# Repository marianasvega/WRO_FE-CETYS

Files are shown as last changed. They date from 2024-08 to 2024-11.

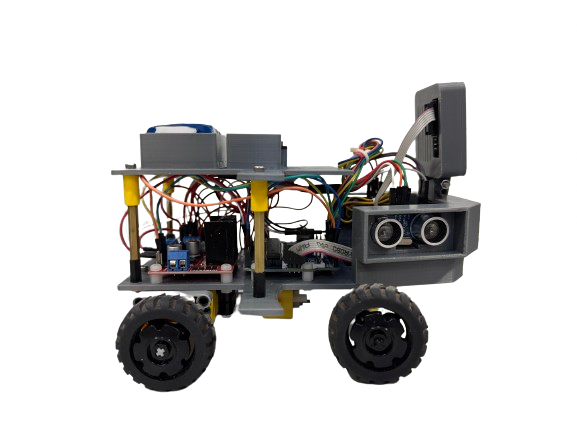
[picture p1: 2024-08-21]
Vehicle Photos/MEXICAN NATIONAL COMPETITION/Right_Side_ViewS.png

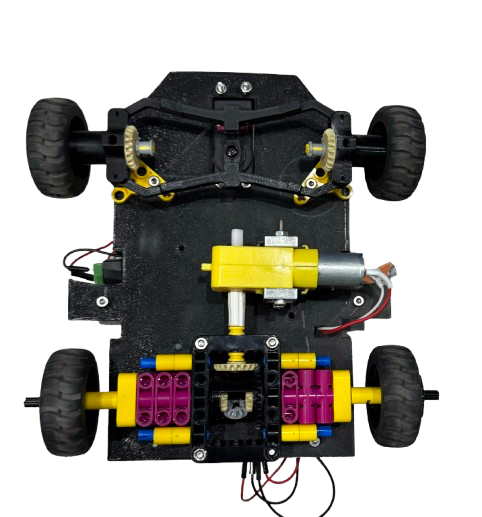
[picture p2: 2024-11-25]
Vehicle Photos/TÜRKIYE INTERNATIONAL COMPETITION/Bottom_View.png

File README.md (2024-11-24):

** **

# CETYS FUTURE ENGINEERS 2024 🤖

This is the official repository for the CETYS Team that participated in the Future Engineers category at the 2024 Mexican National and will soon compete in the International Final in Izmir, Türkiye! Here we will upload all of the processes, improvements, and results regarding our autonomous vehicle, as well as a full report on the code used and its electrical components.
  
**Team Members:** Mariana Sofia Vega Contreras, Claudio Iván López Valle & Mariana Flores Martínez.

CETYS 1 (1920 x 800 px) (1920 x 500 px)

<br>

** **

# Content
* `Models` Files for models used by 3D printers to produce the vehicle elements.
* `Others` Links of videos to understand how to prepare the vehicle for the competition. 
* `Schemes` Diagrams of the electromechanical components used in the vehicle and how they connect.
* `Src` Contains source codes for all components which were programmed to participate in the competition.
* `Team Photos` Contains 2 photos of the team.
* `Vehicle Photos` Contains 6 photos of the vehicle.
* `Video` Contains the link to a video where a driving demonstration exists.
<br>

** **

# Introduction 👷‍♀👨‍💻👩‍🔧
<br>

<div style="display: flex; align-items: flex-start;">
  ARTURO
  <p><be>This report outlines the design, development, and performance of Arturo, the autonomous vehicle developed by our team, the CETYS Future Engineers, for the 2024 World Robot Olympiad. This document will provide a comprehensive overview of our previous work in the Mexican national competition, where we successfully showcased our prototype and the iterative improvements we made in preparation for the international championship in Türkiye.
</p>
</div>
<br>
<br>

** **

# Electronic components

| Component | Quantity |
| --- | :---: |
| **ESP-WROOM-32** | 1 |
| **Bread Board Mini** | 1 |
| **Servo HS-322HD** | 1 |
| **Ultrasonic Sensor HC-SR04** | 5 | 
| **Faulhaber-type DC Motor** | 1 |
| **H-bridge Motor Driver L298N** | 1 |
| **Pushbutton** | 1 |
| **11.1V Battery 4000mAh** | 1 |
| **7.4V Battery 1000mAh** | 1 |
| **330Ω Resistor** | 1 |
| **HuskyLens Camera** | 1 |
| **Switch Button Interruptor KCD1**  | 2 |
| **Gyro + Accelerometer MPU-6050** | 1 |

<br>

** **

# Mechanism explanation

### `Robot´s Vision (HuskyLens Camera) 📷`

<div style="display: flex; align-items: flex-start;">
  HuskyLens Camera
  <p>
    For our vehicle to better detect the obstacles on the rink, we decided to upgrade from the Pixy2 Camera to the HuskyLens Camera. This decision was made after much research and due to a compatibility problem we had while trying to program the Pixy2 with the ESP32. HuskyLens is an AI-powered vision sensor designed for a wide range of applications, including robotics, DIY electronics, and IoT projects such as this. This compact camera module integrates machine learning algorithms to perform tasks like face detection, object tracking, color identification, and gesture recognition, enabling intuitive interaction and intelligent automation. For this component, we used the following code (the syntax of the commands corresponds to the HuskyLens Arduino library):
  </p>
</div>

```ruby
if (huskylens.request()) {                                        // REQUEST DETECTED OBJECTS FROM CAMERA //
    for (int i = 0; i < huskylens.countBlocks(); i++) {
      HUSKYLENSResult result = huskylens.getBlock(i);             // CHECK IF THE DETECTED COLOR IS RED OR GREEN //
      if (result.ID == 1) {                                       // GREEN COLOR (BASED ON OUR PROGRAMMING) //
        Serial.println("Detected Green Object!");
        Serial.println("X Position: " + String(result.xCenter));
      }
      else if (result.ID == 2) {                                  // RED COLOR (BASED ON OUR PROGRAMMING) //
        Serial.println("Detected Red Object!");
        Serial.println("X Position: " + String(result.xCenter));
     }
   }
 }
```

<br>
  
One of the main benefits of HuskyLens is its ability to bring sophisticated AI and machine learning capabilities to users without requiring deep technical expertise. It can also perform real-time tasks without an internet connection, leading to faster response times and reduced latency. Finally, it is compatible with various microcontrollers and development platforms, such as Arduino, ESP32, and Raspberry Pi, and supports multiple communication protocols, including UART and I2C.

<br>
<br>
  
### `Front Tire Axle (Ackerman Steering and HS-322HD Servo) 🛞`

During the Mexican National Competition, we observed that our vehicle needed a better steering system that could round corners with much more facility and precision. After much research, we learned about a mechanism named the Ackerman Steering Principle. When a vehicle turns, the inner wheel follows a tighter path than the outer wheel. To ensure smooth turning without excessive tire wear or slipping, the inner wheel needs to turn at a sharper angle than the outer wheel. This is precisely what the Ackermann geometry achieves.

<br>

<div style="display: flex; align-items: flex-start;">
  Four-Wheel Steering Design
  <p>
    <strong>Figure 1:</strong> Design and Development of Four-Wheel Steering for All Terrain Vehicle (Vishnu 2020):  
    When a driver turns the steering wheel, the motion is passed through the steering column to the steering gear. This gear changes the rotation into a pushing or pulling movement, which is sent to the tie rods. The tie rods then adjust the steering arms connected to the wheels. This setup ensures that the inside wheel turns at a sharper angle than the outside wheel, helping the vehicle turn more efficiently while reducing tire wear and slip.
  </p>
</div>

<br>

> [!NOTE]
>For the STL files to print the Ackerman system we used, visit the following link for it is NOT of our property and we give full credits to the owner: [https://github.com/KarenWon9/WRO-FI-Team-Spark](url)

<br>

<div style="display: flex; align-items: flex-start;">
  HS-322HD Servo
  <p>
    On the other hand, the HS-322HD is a popular heavy-duty servo known for its durability and performance, and without it, our vehicle would have no direction. It features Hitec's Karbonite gear train, which is significantly stronger than standard nylon gears, making it suitable for various applications. With a good balance of speed and torque, the HS-322HD is often used in RC airplanes, helicopters, and other models. To use the servo in the code, it is necessary to include the "Servo.h" library. After that, all that it takes to change the servo's angle is the following command.
  </p>
</div>

```ruby
servo.write(45);
```
<br>
<br>

### `Ultrasonic Sensors (HC-SR04) 📏`
The primary challenge in this category is navigating corners and avoiding collisions with walls. To address this, we employed the HSR04 ultrasonic sensor, which operates by emitting ultrasonic pulses and measuring the time it takes for the echoes to return after bouncing off an object. This time delay is then converted into a distance measurement, allowing the sensor to detect objects and measure distances with precision accurately. 

<br>

<div style="display: flex; align-items: flex-start;">
  Ultrasonic Sensor
  <p>
    Our autonomous vehicle uses 3 ultrasonic sensors in the front part. We have a middle sensor that is always facing forward (parallel to any wall when driving straight), the other two are positioned perpendicular to the first, one on the left side and the other to the right. These two “side” ultrasonic sensors are what help us know at any moment if we're driving too close to a wall or if a turn is near. To keep our driving as straight as possible, we added two extra ultrasonics, each one collinear to a side sensor. For a better understanding of how each sensor is positioned, please visit our <strong>Vehicle Images</strong> section.
  </p>
</div>

<br>

The HSR04 sensor typically has a range of 2 centimeters to 4 meters and is favored for its ease of integration with microcontrollers like Arduino due to its simplicity and cost-effectiveness. Its compact design and straightforward interface make it ideal for applications involving obstacle detection, proximity sensing, and distance measurement in various DIY and industrial projects. To process and interpret this signal given in centimeters, we use the following code:

<br>

```ruby
long DisCalc(int TP, int EP) {

  digitalWrite(TP, LOW);                    // CLEAR THE TRIG PIN //
  delayMicroseconds(2); 

  digitalWrite(TP, HIGH);                   // SET THE TRIG PIN HIGH FOR 10 MICROSECONDS //
  delayMicroseconds(10);
  digitalWrite(TP, LOW);

  long duration = pulseIn(EP, HIGH);        // READ THE ECHO PIN AND CALCULATE THE DIRECTION //

  long distance = duration * 0.034 / 2;     // CALCULATE THE DISTANCE IN CENTIMETERS //

  return distance;
}
```
<br>

> [!NOTE]
>The "distance" variable represents the distance from the sensor to the wall. It’s computed by multiplying the duration of the echo by the speed of sound (0.034 cm/µs) and dividing by 2 to account for the round trip of the sound wave. This distance helps in determining when to navigate around obstacles.
<br>
<br>

### `Gyro + Accelerometer (MPU-6050) 📐`
In both the open and the obstacle avoidance challenge, the vehicle must automatically stop after completing three full rounds. To accomplish this, we decided to use a combination of an accelerometer and a gyroscope. The accelerometer tracks the vehicle’s movement and angle, helping confirm its motion along the course, while the gyroscope measures precise angular changes, allowing us to identify each turn with accuracy.

<br>

<div style="display: flex; align-items: flex-start;">
  MPU-6050 Gyroscope
  <p>
    Using the gyroscope, each directional change of the vehicle is logged based on its orientation. Specifically, a 90° change corresponds to a left turn, while a -90° change corresponds to a right turn. This setup allows us to monitor every turn the vehicle makes throughout its path. By counting these 90° increments, we can accurately detect each completed round, ensuring reliable tracking over multiple rounds. Once the vehicle has completed three rounds, this data is used to signal an automatic stop.
  </p>
</div>

<br>

To achieve this, the following code uses the MPU6050.h library to read data from the MPU6050 gyroscope and accelerometer. It tracks changes in the yaw angle, incrementing by 90° with each turn. By monitoring these increments, the program counts full rotations and stops the vehicle after it reaches the target round count:

<br>

```ruby
MPU6050 mpu;                 // INITIALIZE MPU 6050 //

float ANG = 0;               // VARIABLE TO STORE YAW ANGLE //
unsigned long lastTime = 0;  // STORE THE LAST TIME TIME readYawAngle WAS CALLED //

void setup() {
  Serial.begin(115200);
  
  Wire.begin(21, 22);        // INITIALIZE I2C - SDA, SCL FOR ESP32 //

  // INITIALIZE MPU6050 ACCELEROMETER/GYRO // 
  if (!mpu.begin(MPU6050_SCALE_2000DPS, MPU6050_RANGE_2G)) {
    Serial.println("Could not find MPU6050");
    while (1);
  }
  Serial.println("MPU6050 initialized");
  
  mpu.calibrateGyro();       // SET ZERO REFERENCE FOR YAW //

  lastTime = millis();       // INITIALIZE lastTime //
}

void loop() {
  ANG = readYawAngle();      // GET THE CURRENT YAW ANGLE //
  Serial.print("Yaw Angle: ");
  Serial.println(ANG);

  // CHECK IF A 90-DEGREE TURN HAS BEEN MADE //
  if (ANG >= 90.0 || ANG <= -90.0) {
    Serial.println("90-degree turn detected!");
    ANG = 0;                 // RESET YAW ANGLE //
}
delay(10);
}

float readYawAngle() {
  Vector rawGyro = mpu.readRawGyro();
  float YR = rawGyro.ZAxis/130.0;       // CORRECT SENSITIVITY FOR 2000DPS RANGE //
  
  unsigned long currentTime = millis(); // CALCULATE TIME DIFFERENCE IN SECONDS //
  float dt = (currentTime - lastTime)/1000.0; // CONVERT TO SECONDS //
  lastTime = currentTime;                     // UPDATE lastTime FOR NEXT CALL //  
  
  float driftRate = .02 / 3.0;   // DRIFT RATE OF 1 DEGREE EVERY 3 SECONDS //
  // INTEGRATE YAW RATE OVER TIME TO GET YAW ANGLE //
  ANG += YR * dt;
  ANG -= driftRate * dt;         // Subtract the estimated drift

  return ANG;
}
```
<br>
<br>

### `Rear Tire Axle (Faulhaber MOT-165 and LEGO Differential) ⚙️`
The most crucial mechanism of any vehicle is its drive system, and we aimed to replicate this as closely as possible. After some trial and error during the building process, we decided to incorporate a LEGO differential kit to simulate real-world driving dynamics (you can find the kit [here](https://www.amazon.com/dp/B0C4LFN1HD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)). In the video provided, you can see our custom differential in action, where we designed and attached additional LEGO components. For a step-by-step guide on building your own, please refer to the "Others" folder in this repository.

<br>

<div align="center">
  <video width="340" src="https://github.com/user-attachments/assets/d7e541df-3d19-4036-9754-b866e7325a33
" controls width="600">
  </video>
</div>

<br>

> [!NOTE]
>If you want to learn how a differential works you can watch [this](https://www.youtube.com/watch?v=K4JhruinbWc) video, basically a differential gear allows wheels on the same axle to rotate at different speeds. It works by using a set of gears to distribute torque between the wheels, enabling them to turn at different rates, which is essential for smooth cornering. If 𝑇 is the total torque supplied by the engine to the differential, and it is divided between the two wheels, then the torque 𝑇<sub>1</sub> on one wheel and 𝑇<sub>2</sub> on the other wheel satisfy 𝑇 = 𝑇<sub>1</sub> + 𝑇<sub>2</sub>.

<br>

The motor used in this mechanism is a Faulhaber MOT-165. We opted for this motor because it usually operates at voltages ranging from 6V to 12V, the speed of the motor varies with voltage and load conditions, but it is designed to achieve high RPM (revolutions per minute), and it provides a modest amount of torque, suitable for small, precise applications. It is important to mention that the motor and its driver, the L298N dual H-Bridge, have their power supply, a _**Li-Po battery of 1000 mAh and 7.4V**_.
<br>

<br>

** **

## How it all comes together (explaining the code) 💻
<br>

We will now discuss how all of the previously mentioned mechanisms assemble together in our final code (Open and Obstacle Challenge). Before we start, we will show all of the functions used along the code to use as reference for when they appear next.

```ruby
int DisCalc(int TP, int EP) {                                                // ULTRASONIC BASIC CODE //

  long duration = -1;
  int reading = 120; 
  int cont = 0;

  while (cont < 5) { 
    digitalWrite(TP, LOW);
    delayMicroseconds(2);
    digitalWrite(TP, HIGH);
    delayMicroseconds(10);
    digitalWrite(TP, LOW);

    duration = pulseIn(EP, HIGH, 10000); 

    if (duration > 0) {
      reading = duration * 0.034 / 2; 
      break;  
    }

    cont++;  
  }

  return reading;

}

void printDistances(long distanceLeft, long distanceHleft, long distanceMid, long distanceHright, long distanceRight){

  Serial.print("Dis Left: ");
  Serial.print(distanceLeft);
  Serial.print(" Dis MidLeft: ");
  Serial.print(distanceHleft);
  Serial.print(" Dis Mid: ");
  Serial.print(distanceMid);
  Serial.print(" Dis MidRight: ");
  Serial.print(distanceHright);
  Serial.print(" Dis Right: ");
  Serial.println(distanceRight);

}

void printDistancesM(long distanceMid) {

  Serial.print(" Dis Mid: ");
  Serial.println(distanceMid);

}

float readYawAngle(int X) {                                                  // GYROSCOPE BASIC CODE //

  Vector rawGyro = mpu.readRawGyro();
  float YR = rawGyro.ZAxis / 131.0; 
  
  if (X == 0){
    unsigned long currentTime = millis();
    float dt = (currentTime - lastTime) / 1000.0; 
    lastTime = currentTime; 

    ANG += YR * dt;
    ANG -=   .02;  
  }

  else if (X == 1){
    unsigned long currentTime = millis();
    float dt = (currentTime - lastTime) / 1000.0; 
    lastTime = currentTime; 
  
    ANG += YR * dt;
    ANG +=   0.019;  
  }

  else if (X == 2) {
    unsigned long currentTime = millis();
    float dt = (currentTime - lastTime) / 1000.0; 
    lastTime = currentTime; 
  
    ANG += YR * dt;
    ANG -=   .075;  
  }
  
  return ANG;

}

void GreenO(int X){                                                           // OBJECT DETECTED IS GREEN //

  Serial.println("Detected Green Object!");

  if (X < 90 ){
    while(X < 90){
      SLIGHTLY_LEFT_MAX();
    } 
  }

  else if(X < 158 && X > 90){
    while(X < 158 && X > 90){
      SLIGHTLY_LEFT();
    } 
  }

  else if(X > 158 && X < 240){
    SLIGHTLY_LEFT_MID();
  }

  else if(X > 240){
    SLIGHTLY_LEFT_MIN();
  }

}

void RedO(int X){                                                             // OBJECT DETECTED IS RED //

  Serial.println("Detected Red Object!");

  if (X < 90 ){
    while(X < 90){
      SLIGHTLY_RIGHT_MIN();
    }
  }

  else if(X < 158 && X > 90){
    while(X < 158 && X > 90){
      SLIGHTLY_RIGHT_MID();
    } 
  }

  else if(X > 158 && X < 240){
    while(X > 158 && X < 240){
      SLIGHTLY_RIGHT();
    }
  }

  else if(X > 240){
    while(X > 240){
      SLIGHTLY_RIGHT_MAX();
    }
  }

}

void STRAIGHT(){                                                              // DIFFERENT VELOCITY CONFIGURATIONS //

  servo.write(93);
  digitalWrite(IN1, HIGH);
  digitalWrite(IN2, LOW);
  ledcWrite(ENA, 100);  
  delay(10);

}

void STRAIGHT_SLOW(){

  servo.write(94);
  digitalWrite(IN1, HIGH);
  digitalWrite(IN2, LOW);
  ledcWrite(ENA, 70);  
  delay(10);

}

void RIGHT(){

  servo.write(63);
  digitalWrite(IN1, HIGH);
  digitalWrite(IN2, LOW);
  ledcWrite(ENA, 90);  
  delay(10);

}

void SLIGHTLY_RIGHT(){

  servo.write(79);
  digitalWrite(IN1, HIGH);
  digitalWrite(IN2, LOW);
  ledcWrite(ENA, 90); 
  delay(10);

}

void SLIGHTLY_RIGHT_MAX(){

  servo.write(74);
  digitalWrite(IN1, HIGH);
  digitalWrite(IN2, LOW);
  ledcWrite(ENA, 90);  
  delay(10);

}

void SLIGHTLY_RIGHT_MID(){                     

  servo.write(84);
  digitalWrite(IN1,HIGH);   
  digitalWrite(IN2,LOW);            
  ledcWrite(ENA, 100);  
  delay(10);                

} 

void SLIGHTLY_RIGHT_MIN(){                    

  servo.write(86);
  digitalWrite(IN1,HIGH);   
  digitalWrite(IN2,LOW);         
  ledcWrite(ENA, 100);   
  delay(10);                  

} 

void REVERSE_RIGHT(){

  servo.write(119);
  digitalWrite(IN1, LOW);
  digitalWrite(IN2, HIGH);
  ledcWrite(ENA, 100);  
  delay(10);

}

void LEFT(){

  servo.write(125);
  digitalWrite(IN1, HIGH);
  digitalWrite(IN2, LOW);
  ledcWrite(ENA, 90); 
  delay(10);

}

void SLIGHTLY_LEFT(){

  servo.write(109);
  digitalWrite(IN1, HIGH);
  digitalWrite(IN2, LOW);
  ledcWrite(ENA, 90); 
  delay(10);

}

void SLIGHTLY_LEFT_MAX(){

  servo.write(114);
  digitalWrite(IN1, HIGH);
  digitalWrite(IN2, LOW);
  ledcWrite(ENA, 90);  
  delay(10);

}

void SLIGHTLY_LEFT_MID(){                      

  servo.write(104);
  digitalWrite(IN1,HIGH);   
  digitalWrite(IN2,LOW); 
  ledcWrite(ENA, 100);  
  delay(10);
}

void SLIGHTLY_LEFT_MIN(){                   

  servo.write(102);
  digitalWrite(IN1,HIGH);   
  digitalWrite(IN2,LOW);
  ledcWrite(ENA, 100); 
  delay(10);

}

void REVERSE_LEFT(){

  servo.write(69);
  digitalWrite(IN1, LOW);
  digitalWrite(IN2, HIGH);
  ledcWrite(ENA, 100);  
  delay(10);

}

void STOP(){

  servo.write(94);
  digitalWrite(IN1, LOW);
  digitalWrite(IN2, LOW);
  ledcWrite(ENA, 0);  
  delay(10);

} 

void CORRECT(int d1, int d2, int d3, int d4){                                 // VEHICLE IS TOO CLOSE TO A WALL //

  if (d1 < d4) {
    if (d1 < 23) {
      SLIGHTLY_RIGHT();
    } 
    else if (d2 < 23) {
      SLIGHTLY_RIGHT();
    }      
  }
  
  else if (d4 < d1) {
    if (d4 < 23) {
      SLIGHTLY_LEFT();
    } 
    else if (d3 < 23) {
      SLIGHTLY_LEFT();
    }  

  }

}

void CORRECT1(float ang) { 
 if (ang > 3)
{
  SLIGHTLY_RIGHT_MIN();
}
else if (ang < -3)
{
  SLIGHTLY_LEFT_MIN();
}

}
```
<br>

  1. Now, let´s begin with the main code. First, we check if the button has been pressed. If it hasn´t, the robot must remain still until instructed otherwise.

```ruby
if (digitalRead(buttonPin) == HIGH && cont == 0) {              // START //
  start = true; 
  cont = 1;
  delay(500); 
}

if (digitalRead(buttonPin) == HIGH && cont == 1) {              // STOP //
  start = false;        
  cont = 0;
  delay(500); 
}

if (start == true) {                                            // BUTTON IS PRESSED AND CODE BEGINS //
```
<br>

2. Then, we must check if there is an obstacle present, and swerve to the right condition (left or right).
```ruby

if (huskylens.request()) {                                                  // OBTAIN DATA FROM HUSKYLENS //
  for (int i = 0; i < huskylens.countBlocks(); i++) {
    HUSKYLENSResult result = huskylens.getBlock(i);
    if (result.ID == 1) {                                                   // ID1 = GREEN //
       GreenO(result.xCenter);
    }
    else if (result.ID == 2) {                                              // ID2 = RED //
       RedO(result.xCenter);
    }
  }
}

```
<br>

 3. Then we use our functions to check the distances from the 5 ultrasonic sensors. By receiving this information the vehicle can know if it must move forward, backwards, or give a left/right turn.

```ruby
if (Lap <= 11) {
    DisL = DisCalc(Trig_US, Echo_US1);                                       // CALCULATE DISTANCES AND ANGLE //
    delay(5);
    DisM = DisCalc(Trig_US, Echo_US2);
    delay(5);
    DisR = DisCalc(Trig_US, Echo_US3);
    delay(5);
    DisLA = DisCalc(Trig_US, Echo_USAux1);
    delay(5);
    DisRA = DisCalc(Trig_US, Echo_USAux2);
    delay(5);

    printDistances(DisL, DisLA, DisM, DisRA, DisR);

    ANG = readYawAngle(x);
    Serial.print("Angle: ");
    Serial.println(ANG);

    STRAIGHT();
```
<br>

  4. Now we check if there is in fact a turn, either left or right. While doing the turn, the vehicle must constantly keep checking the distances to avoid false readings. If the turn was not completed, the vehicle must return and correct.

```ruby
  if ((millis() - lastTurnTime) > 3500) {                                 // CHECK TIME SINCE LAST TURN //
      if ((DisM < 75 && DisL > 85) || (DisM < 75 && DisLA > 85)) {          // LEFT TURN //
        for (;;) {
          x = 1;
          ANG = readYawAngle(x);
          Serial.print("Angle: ");
          Serial.println(ANG);

          if (ANG >= 90.0 || ANG <= -90.0) {
            Serial.println("Turn detected!");
            ANG = 0;  
            Lap++;
            lastTurnTime = millis(); 
            break;
          }

          DisM = DisCalc(Trig_US, Echo_US2);
          delay(5);

          printDistancesM(DisM);

          if (DisM < 14) {
            servo.write(69);
            REVERSE_LEFT();
            delay(1300);
            break;
          }

          LEFT();  
        }
      }

      if ((DisM < 75 && DisR > 85) || (DisM < 75 && DisRA > 85)) {          // RIGHT TURN //
        for (;;) {
          x = 2;
          ANG = readYawAngle(x);
          Serial.print("Angle: ");
          Serial.println(ANG);

          if (ANG >= 90.0 || ANG <= -90.0) {
            Serial.println("Turn detected!");
            ANG = 0;  
            Lap++;
            lastTurnTime = millis();  
            break;
          }

          DisM = DisCalc(Trig_US, Echo_US2);
          delay(5);

          printDistancesM(DisM);

          if (DisM < 14) {
            servo.write(120);
            REVERSE_RIGHT();
            delay(1300);
            break;
          }

          RIGHT();  
        }
      }
    }

```
<br>

  5. If the middle distance detected something less than 90 but there wasn´t a turn near, the vehicle must continue straight forward, or in the case that it´s too close to any wall, it must correct.

```ruby
if (DisR < 20 || DisL < 20 || DisRA < 20 || DisLA < 20) {
      CORRECT(DisL, DisLA, DisRA, DisR);
    } else if (ANG > 3 || ANG < -3) {
      CORRECT1(ANG);
    }
  }
else {
    servo.write(94);
    delay(100);
    STRAIGHT();
    delay(1600);

    for (;;) {
      STOP();
    }
  }

```

<br>

** **

# Acknowledgments

We would like to take a space to thank our sponsors, without whom this project could not have come to be. Your help not only made a significant contribution to the progress of this autonomous vehicle but aided in the innovation of technology and design that may very well help other future engineers. We are very grateful for your kindness.

Sincerely, Mariana Flores, Claudio López, and Mariana Vega.

CETYS (1920 x 500 px)

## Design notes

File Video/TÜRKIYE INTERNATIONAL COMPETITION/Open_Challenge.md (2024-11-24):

** **

## Open Challenge⚙️
**Visit the following YouTube link:** [Open challenge demonstration](https://youtu.be/cOm-VNnHiJk)

** **

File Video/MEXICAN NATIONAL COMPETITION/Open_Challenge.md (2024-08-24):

** **

## Open Challenge⚙️
**Visit the following YouTube link:** [Open challenge demonstration](https://youtu.be/UetUEMxAGJ0)

** **

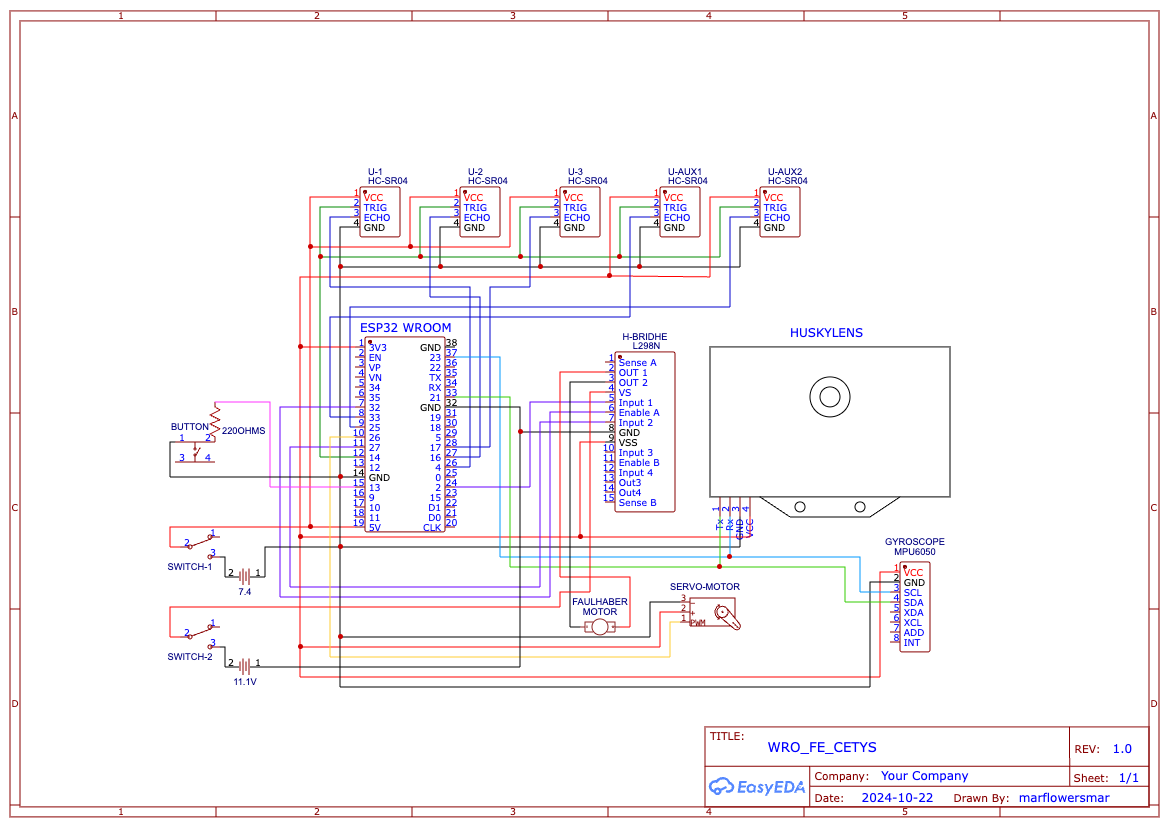
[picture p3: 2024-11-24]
Schemes/TÜRKIYE INTERNATIONAL COMPETITION/Schematic_View.png

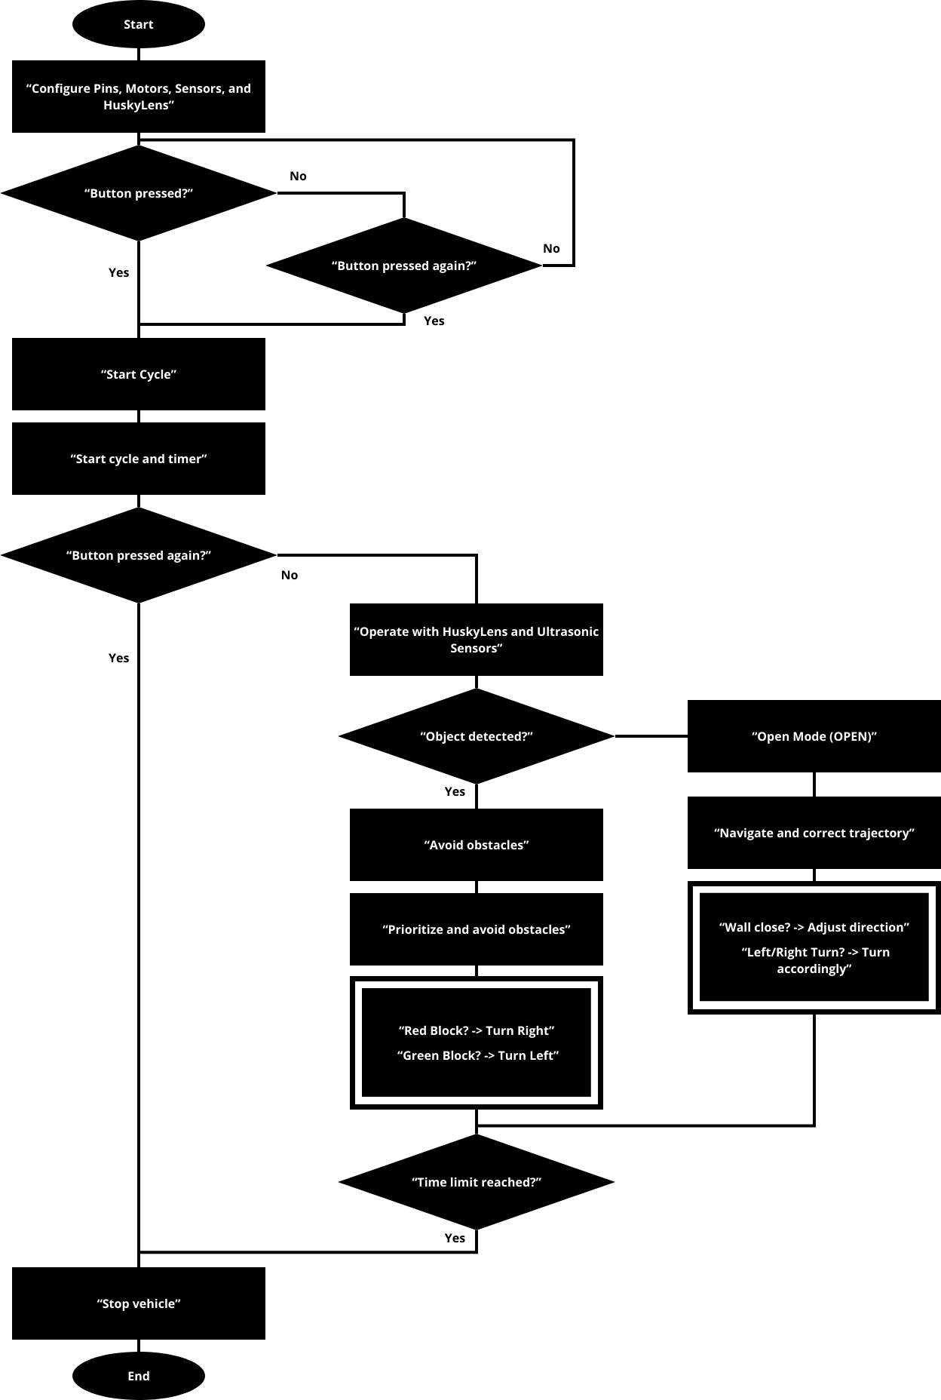
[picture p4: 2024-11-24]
Schemes/TÜRKIYE INTERNATIONAL COMPETITION/Flow_Chart.png

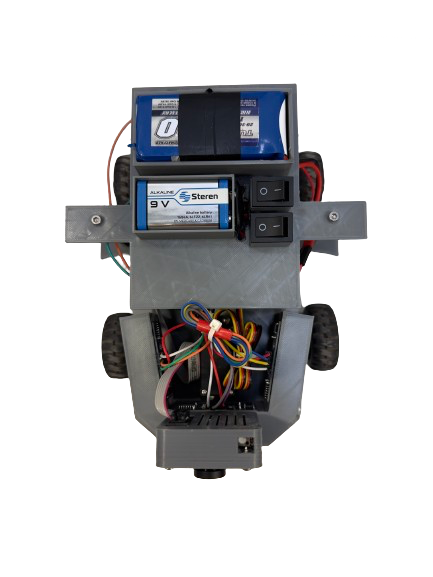
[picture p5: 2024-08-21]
Vehicle Photos/MEXICAN NATIONAL COMPETITION/Top_View.png

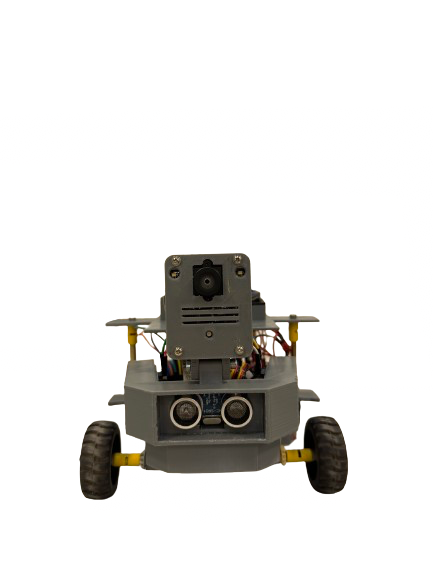
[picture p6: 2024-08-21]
Vehicle Photos/MEXICAN NATIONAL COMPETITION/Front_View.png

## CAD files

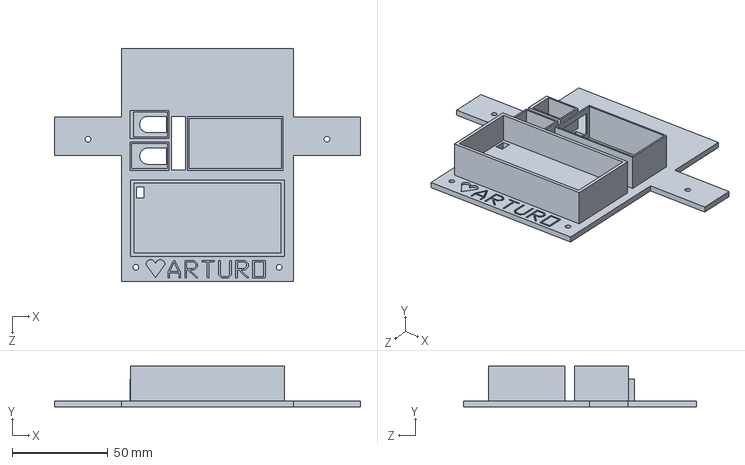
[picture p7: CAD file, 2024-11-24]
Models/MEXICAN NATIONAL COMPETITION/SOLID_PART/Upper_Cover.SLDPRT
160.0 x 21.3 x 122.0 mm

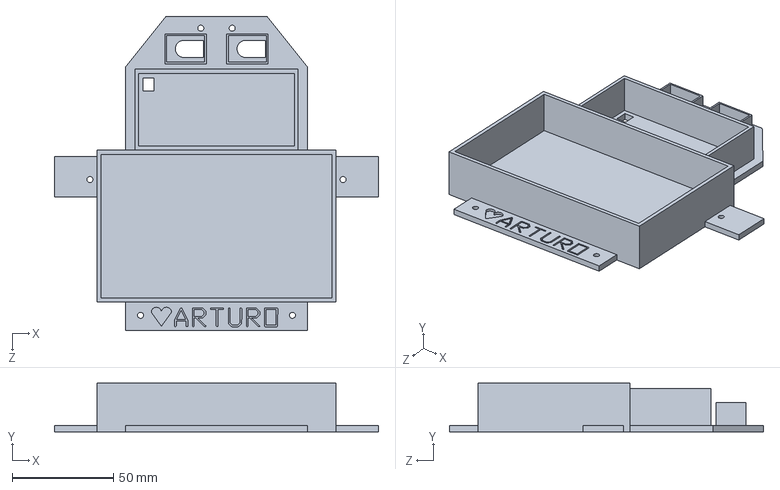
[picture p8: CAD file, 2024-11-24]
Models/TÜRKIYE INTERNATIONAL COMPETITION/SOLID_PART/Upper_Cover.SLDPRT
160.0 x 24.0 x 155.0 mm

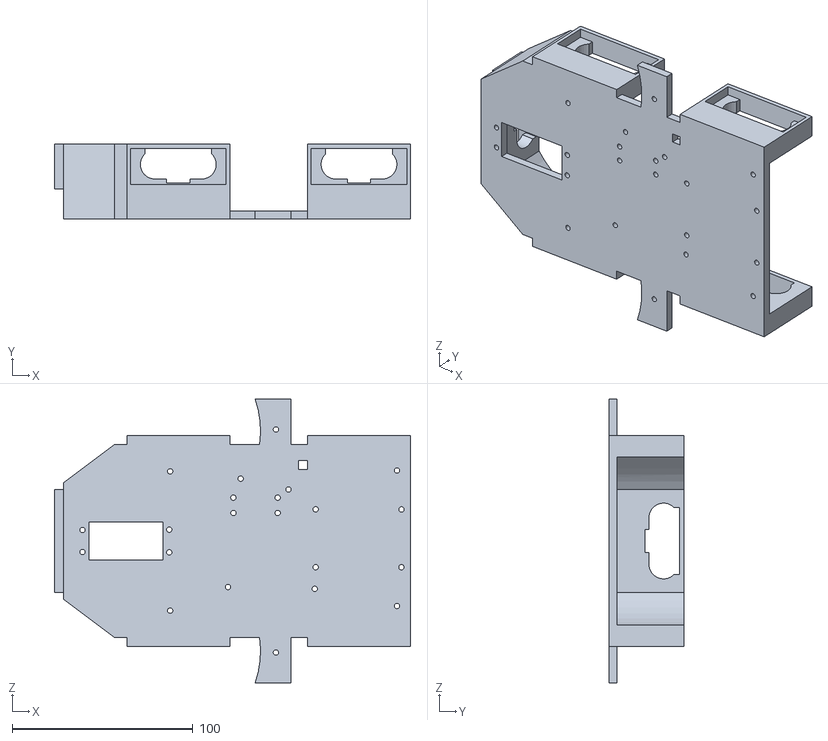
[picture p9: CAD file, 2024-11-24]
Models/TÜRKIYE INTERNATIONAL COMPETITION/STL_CODE/Vehicle_Chassis.STL
197.0 x 41.5 x 157.0

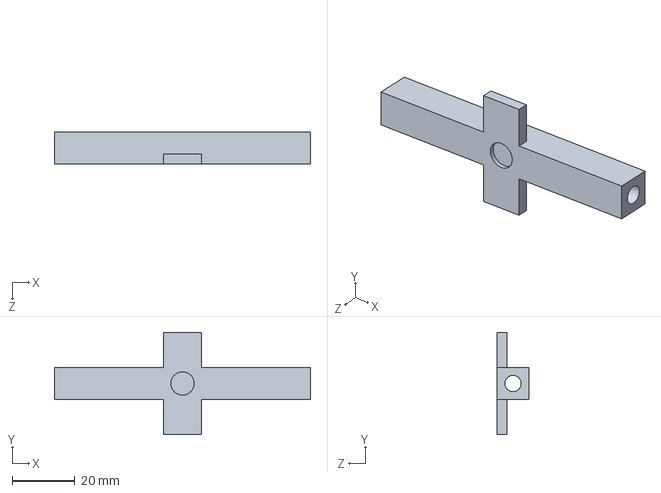
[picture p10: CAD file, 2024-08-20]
Models/MEXICAN NATIONAL COMPETITION/SOLID_PART/Tire_Axl.SLDPRT
81.9 x 32.8 x 10.2 mm

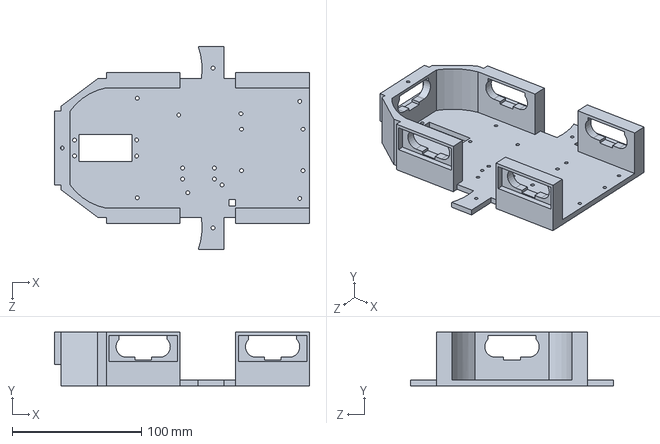
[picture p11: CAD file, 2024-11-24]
Models/TÜRKIYE INTERNATIONAL COMPETITION/SOLID_PART/Vehicle_Chassis.SLDPRT
197.0 x 41.5 x 157.0 mm

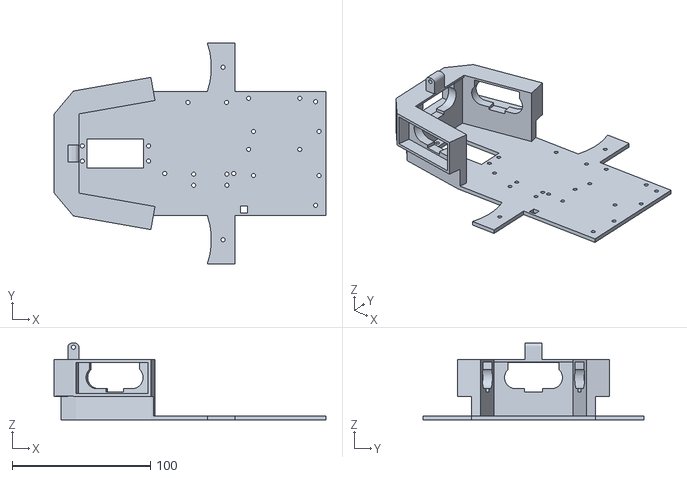
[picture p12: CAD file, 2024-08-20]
Models/MEXICAN NATIONAL COMPETITION/STL_CODE/Vehicle_Chassisl.STL
197.0 x 160.0 x 55.7

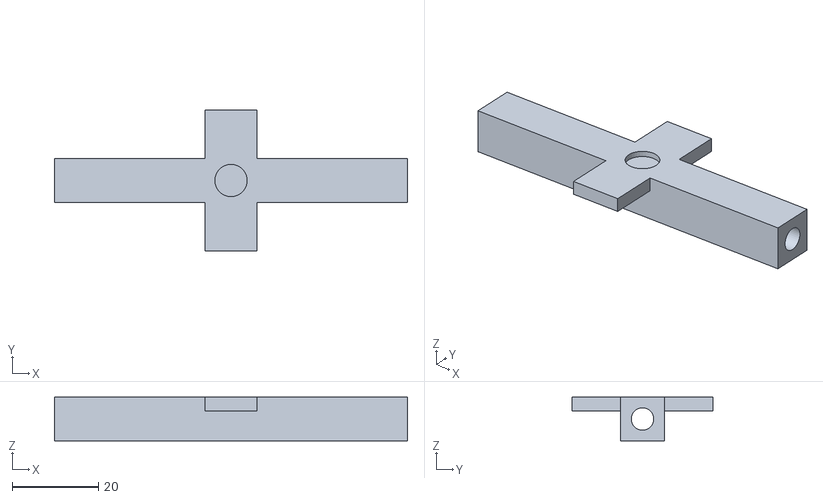
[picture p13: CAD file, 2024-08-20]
Models/MEXICAN NATIONAL COMPETITION/STL_CODE/Tire_Axl.STL
81.9 x 32.8 x 10.2

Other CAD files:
Models/MEXICAN NATIONAL COMPETITION/STL_CODE/Upper_Cosver.STL
Models/MEXICAN NATIONAL COMPETITION/STL_CODE/Upper_Cover.STL
Models/TÜRKIYE INTERNATIONAL COMPETITION/STL_CODE/Upper_Cover.STL
Models/MEXICAN NATIONAL COMPETITION/SOLID_PART/Vehicle_Chassi.SLDPRT
Models/MEXICAN NATIONAL COMPETITION/SOLID_PART/Vehicle_Chassis.SLDPRT

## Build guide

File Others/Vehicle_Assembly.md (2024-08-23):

## Differential Assembly⚙️
**Visit the following YouTube link:** [Differential Assembly](https://youtu.be/wBKvdf76l_8?si=xTCuxnM3gSAiyvXd)
** **

## Chassis Assembly🛞
**Visit the following YouTube link:** [Chassis Assembly](https://youtu.be/u0xRfmP369c)
** **

## Battery Support🔋
**Visit the following YouTube link:** []()

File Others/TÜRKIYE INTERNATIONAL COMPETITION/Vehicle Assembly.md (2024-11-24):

** **

## Differential Assembly⚙️
**Visit the following YouTube link:** [Differential Assembly](https://youtu.be/wBKvdf76l_8?si=xTCuxnM3gSAiyvXd)

** **

## Vehicle Final Assembly🔋
**Visit the following YouTube link:** [Vehicle Final Assembly](https://youtu.be/vljPDZFnR9c)

** **

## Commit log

2024-07-25 Create Ultrasonic_Button_Code
2024-07-25 Update Ultrasonic_Button_Code
2024-07-31 Create Camera_Obstacles_Code
2024-07-31 Update Camera_Obstacles_Code
2024-08-19 Create Circuit_Schematic_View
2024-08-19 Circuit Schematic View
2024-08-19 Add files via upload
    This schematic provides a visual representation of all the key electronic components involved in the vehicle's operation, except for the Pixy Camera (which connects to the ICSP pin on the Arduino), t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
    For more detailed information about the electronic components and their connections, please refer to the README section.
2024-08-19 Add files via upload
    This schematic provides a visual representation of all the key electronic components involved in the vehicle's operation, except for the Pixy Camera(connected to the ICSP pin on the Arduino), two Swi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
2024-08-20 Schematic view
2024-08-20 Create Schematic View
2024-08-20 Description
    For more detailed information about the electronic components please refer to the README section.
    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
2024-08-20 STL Code
2024-08-20 Rename Tire_Axle.SLDPRT to Tire Axle
2024-08-20 Tire Axle
    [Tire_Axle.SLDPRT]
2024-08-20 Vehicle Chasis
    [Vehicle_Chasis.SLDPRT]
2024-08-20 Create STL Code
2024-08-21 Upper Cover
    [Upper_Cover.SLDPRT]
2024-08-21 Vehicle Chassis
    [Vehicle_Chassis.SLDPRT]
2024-08-21 Description
    This schematic provides a visual representation of all the key electronic components involved in the vehicle's operation, except for the Pixy Camera (connected to the ICSP pin on the Arduino), two Sw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
2024-08-22 Differential Assembly
2024-08-22 Vehicle Assembly
2024-08-23 VEHICLE ASSEMBLY.md
2024-08-30 Description
    This flow chart is a graphic representation of the Arduino code, it mainly includes de logic of the vehicle operation.
2024-11-07 Flow Chart
2024-11-07 Description
    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
2024-11-07 Create STL Files
2024-11-24 Create Vehicle Assembly.md
